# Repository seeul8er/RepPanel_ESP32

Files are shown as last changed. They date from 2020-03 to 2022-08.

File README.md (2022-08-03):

# RepPanel

## New Version HWv2 available
[Check out the new version RepPanel HWv2 for RepRap-based 3D Printers! Improved performance with ready to flash hardware from your local supplier.](https://reppanel.com)

## Older HWv1 version
A simple user interface for Duet/RepRap based 3D printers. Optimized for 3.5" touch
panels controlled via SPI & I²C using an ESP32.

Supports wireless connection or wired via UART/PanelDue port.

An open source alternative to the PanelDue.
  - Cheap (~18€ display + 7€ ESP32)
  - Beautifully dark
  - Compact and easy to use
  - Support for most operations required to set up a 3D print
  - Wireless connection - portable with power bar
  - PanelDue-port/UART connection

The all-in-one module is currently not available but you can give me an idea on how much interest there is. The module will be ready to use and thinner than a DIY solution. It includes a custom board, display and more capable ESP32 (more storage for directory listings etc.). I would try to get the price somewhere ~50-60€ + shipping from Germany. Click the link above and enter your email to get notified when a module becomes available. Thanks!

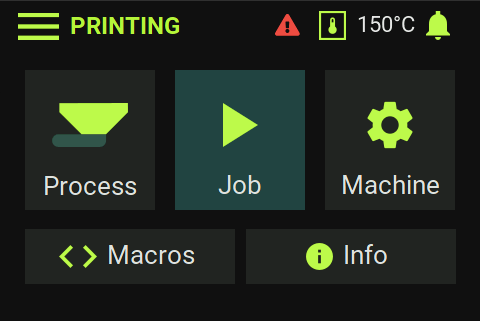
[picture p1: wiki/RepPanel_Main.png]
RepPanel main menu


## Features
Since RepPanel boots in ~1 second you can start setting up your printer in no time and with no additional hardware.
No need to get the laptop and log in to DuetWebControl. No need to get mad over using WebControl in your smartphones
browser.

 - Start, Stop, Pause & Resume print jobs based of Duets SD card
 - Simulate print jobs
 - Delete print jobs
 - Run macros (no dictionary support yet)
 - Home X, Y, Z or All axis
 - Set extruder fan speed
 - Load/Unload filament per tool
 - Set bed temperatures
 - Set tool temperatures
 - Monitor temperatures
 - Monitor print job:
   - Percent complete
   - Duration
   - Elapsed time (based of simulation, otherwise from file)
   - Job name
   - Current layer
 - Run manual and automated bed leveling
 - Automatic reconnection
 - Low latency
 - Screen Saver feature
 - Support for RRF 3.4+ Object Model

First release of RepPanel (https://youtu.be/FfghWz1Lrw4)  
First test of RepPanel (https://www.youtube.com/watch?v=39FKTUVjrxc)

## What this project is not
A full replacement for the DuetWebControl interface.

## Supported Hardware/Software
The RepPanel project is based on the [LVGL port for the ESP32](https://github.com/lvgl/lv_port_esp32/tree/c1f43bfb090df293059ab52baabbdbdd8df00712).
In theory this means all displays and touch controllers supported by the **lv_port_esp32** project are also supported
by RepPanel.

### Tested Hardware
The listed hardware below is tested and pre-compiled images are available under GitHub releases.

#### Hardware v1 (HWv1) platform
  - ESP32 DevKit without external RAM
  - [ER-TFTM035-6 display with capacitive touch screen, 4-Wire SPI, No font chip required](https://www.buydisplay.com/lcd-3-5-inch-320x480-tft-display-module-optl-touch-screen-w-breakout-board)

**Beware:** There are numerous version of the ER-TFT035-6. You must choose the one with the SPI interface. Do not get the arduino shield version (no SPI config). The version with the screen breakout board is sufficient.**  
Other display modules with a resolution of 480x320 should also work as long as they are supported by `lv_port_esp32`  
As of now RepPanel is optimized for 3.5" displays with a resolution of 480x320 pixels. The display is connected via SPI.

#### Hardware v2 (HWv2) platform
  - coming soon
  
### Differences between HWv1 & HWv2
coming soon

**Tested Firmware**
  - Duet2 WiFi running RepRap Firmware v3.0, v3.1, v3.2, v3.3 and corresponding Duet2WebControl
  - Duet3D + SBC is not supported via Wifi - only via the PanelDue serial port (wired connection)

## Installation
Use ready made images or compile yourself.

### Compile yourself

#### Set up ESP-IDF

[Follow instructions](https://docs.espressif.com/projects/esp-idf/en/v4.0/get-started/index.html#step-1-install-prerequisites) on offical Espressif site.  
ESP-IDF v4.0 is officially supported. ESP-IDF v4.3 is officially supported for the HWv2 electronics platform.

#### Clone Project

```bash
git clone --recurse-submodules https://github.com/seeul8er/RepPanel_ESP32
```
LVGL v7 is not supported. Last tested release of `lv_port_esp32` is commit `a76a3d5d9225d0cfb92c896b6b0f1867b62aa2b6`.
The project is linked against a fork to keep the legacy support and be able to fix bugs.

#### Configure Project

From its root run:
```bash
idf.py menuconfig
```
Under ``Component configuration`` you can change the supported TFT and Touchcontroller configuration and RepPanel 
specific settings.  

**See [Custom LVGL port for the ESP32](https://github.com/seeul8er/lv_port_esp32/tree/c1f43bfb090df293059ab52baabbdbdd8df00712) for further and more detailed instructions.**

#### Compile & Flash
```bash
idf.py build
idf.py -p (YOUR PORT) flash
```
**See [LVGL port for the ESP32](https://github.com/lvgl/lv_port_esp32/tree/c1f43bfb090df293059ab52baabbdbdd8df00712) for further and more detailed instructions.**

### Use ready made images
Ready made images are only available for selected hardware combinations! Please compile the project by yourself in
case you use different hardware or want a different pin connection layout

Check out [releases](https://github.com/seeul8er/RepPanel_ESP32/releases) for compiled binaries.

### Wiring ER-TFTM035-6 to the ESP32 DevKit (HWv1)

**Beware:** The available development boards have different pin configurations. Some have GND & 3.3V at the bottom. Others at the top.

Pin configuration of ready made images:
| **Pin Number ESP32 ** |  **Pin Number ER-TFTM035-6** | **Function** | **Description** | 
|:---:|:--:|:---: |:---: |
| VCC 3.3V |  2 | Power supply | Match TFT voltage with ESP32 pin | 
| GND | 1  | GND | Ground | 
| GPIO 13 | 27 | MOSI | Data line to TFT | 
| GPIO 14 | 24 | SCL | SPI CLK for TFT | 
| GPIO 15 | 23 | Slave Select | SPI | 
| GPIO 22 | 30 | SCL | I²C - touch | 
| GPIO 21 | 31 | SDA | I²C - touch | 
| GPIO 4 | 21 | Reset | TFT related | 
| GPIO 2 | 25 | Data | TFT related | 
| GPIO 27 | 29 | Backlight | Turn on/off TFT backlight | 
| GPIO 17 |  - | UART TX | Connect to RX PanelDue port  | 
| GPIO 16 |  - | UART RX | Connect to TX PanelDue port  |

## Screenshots
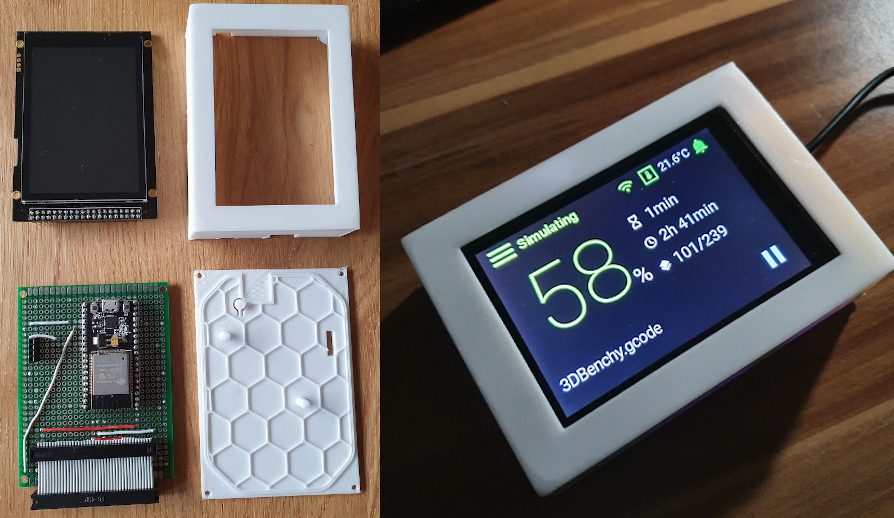
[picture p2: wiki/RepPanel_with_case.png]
RepPanel with case

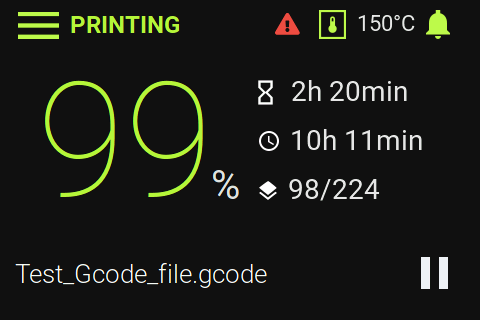
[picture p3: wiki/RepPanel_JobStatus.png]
RepPanel print job status

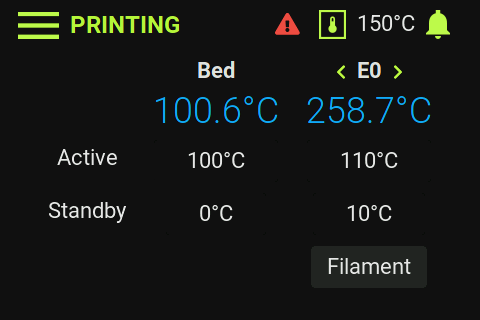
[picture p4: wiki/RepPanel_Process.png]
RepPanel process menu

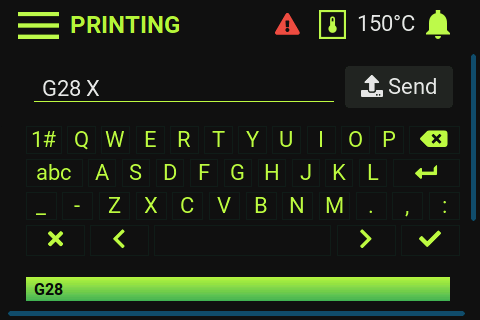
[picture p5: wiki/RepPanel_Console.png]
RepPanel console

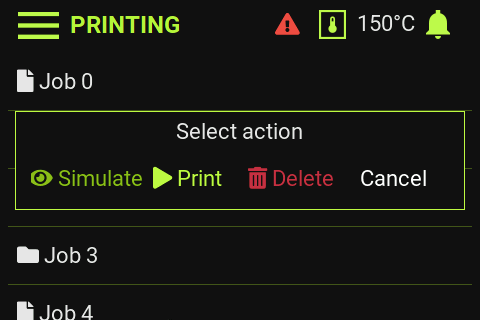
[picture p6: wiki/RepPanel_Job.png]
RepPanel start print dialog


## For Developers
[Check out the simulator project.](https://github.com/seeul8er/RepPanel_sim) Simulates the RepPanel GUI on Desktop computers for more efficient testing and implementation.

Use the provided for of lvgl for ESP32. This one contains the supported version of LVGL with some additional config options regarding the screen saver timeout. It is the only one maintained for RepPanel.

**Custom changes to lv_conf.h**  
Copy file content of `main/lv_conf_back.h` over to `externals/lv_port_esp32/components/lvgl/lv_conf.h`.  
Or simply add:
- Set `LV_USE_USER_DATA 1`
- Set `LV_MEM_SIZE    (17U * 1024U)` to free up unused RAM
- Add `#define LV_USE_THEME_REP_PANEL_DARK 1`
- `CONFIG_LVGL_FONT_ROBOTO16` & `CONFIG_LVGL_FONT_ROBOTO22` must be activated
- Add
```C
#define LV_FONT_CUSTOM_DECLARE  LV_FONT_DECLARE(reppanel_font_roboto_bold_16) \
                                       LV_FONT_DECLARE(reppanel_font_roboto_bold_18) \
                                       LV_FONT_DECLARE(reppanel_font_roboto_bold_24) \
                                       LV_FONT_DECLARE(reppanel_font_roboto_regular_26) \
                                       LV_FONT_DECLARE(reppanel_font_roboto_light_26) \
                                       LV_FONT_DECLARE(reppanel_font_roboto_thin_numeric_160) \
                                       LV_FONT_DECLARE(reppanel_font_roboto_regular_percent_40)
```

**Compilation options for different hardware platforms**
- esp-idf 4.0.x for ER-TFTM035-6 and other ILI9488 based displays (later esp-idf versions cause rendering artifacts)
- esp-idf 4.0.x or 4.3.x for ST7796s based displays

## Known Limitations
- Multiple tools supported but not tested
- Auto swap from UART to WiFi connection might take up to 10s
- Entries per directory listing limited to 24 for jobs and macros for ESP32 modules without external RAM
- Directory path limited to 160 characters for ESP32 modules without external RAM
- Filament listing (all filament names separated by one character) limited to 1014
- No support for Duet3 + SBC via Wifi because of a different API
  - Workaround: Use wired UART/PanelDue connection
- Can not list all files within a directory in case DuetWebControl API requires multiple requests per listing
  - Workaround: Delete files to reduce file count to make all files fit within one response

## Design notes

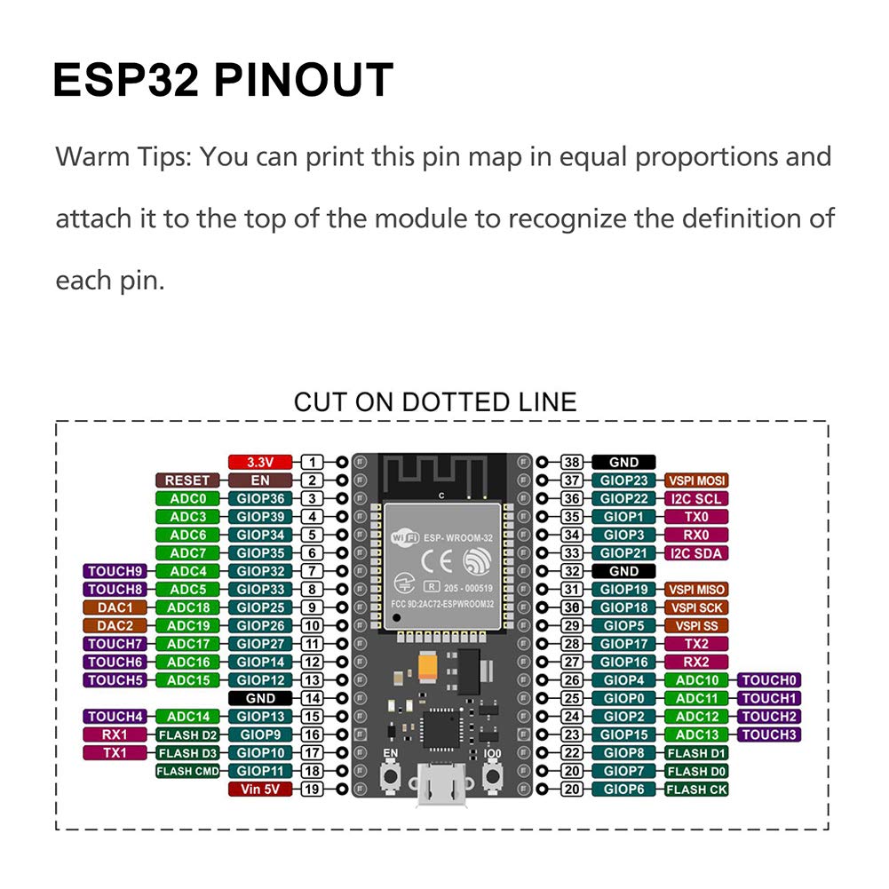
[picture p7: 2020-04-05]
wiki/NodeMCU_ESP32_Pinout.jpg

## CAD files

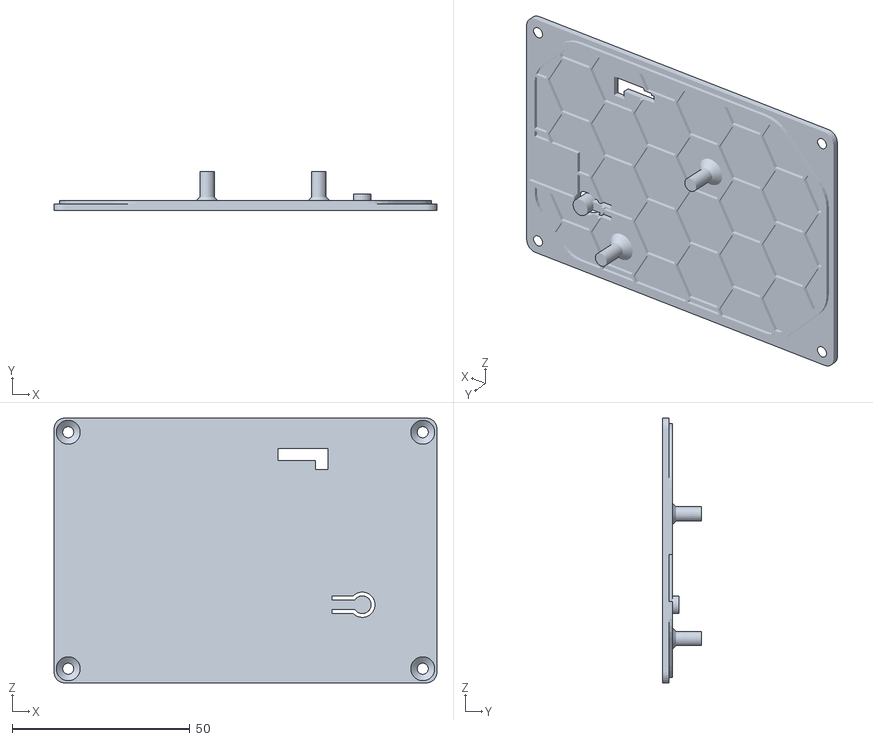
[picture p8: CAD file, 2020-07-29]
case/reppanelcover_back_v1_3.stl
107.7 x 10.9 x 74.5

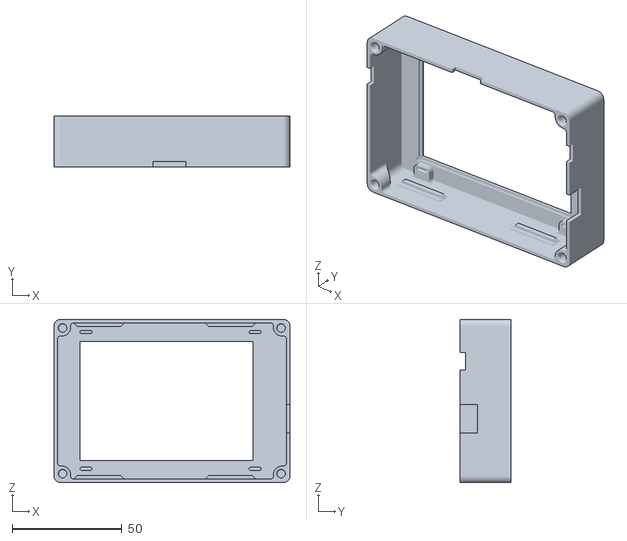
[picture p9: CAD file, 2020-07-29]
case/reppanelcover_front_v1_3.stl
107.7 x 23.4 x 74.5

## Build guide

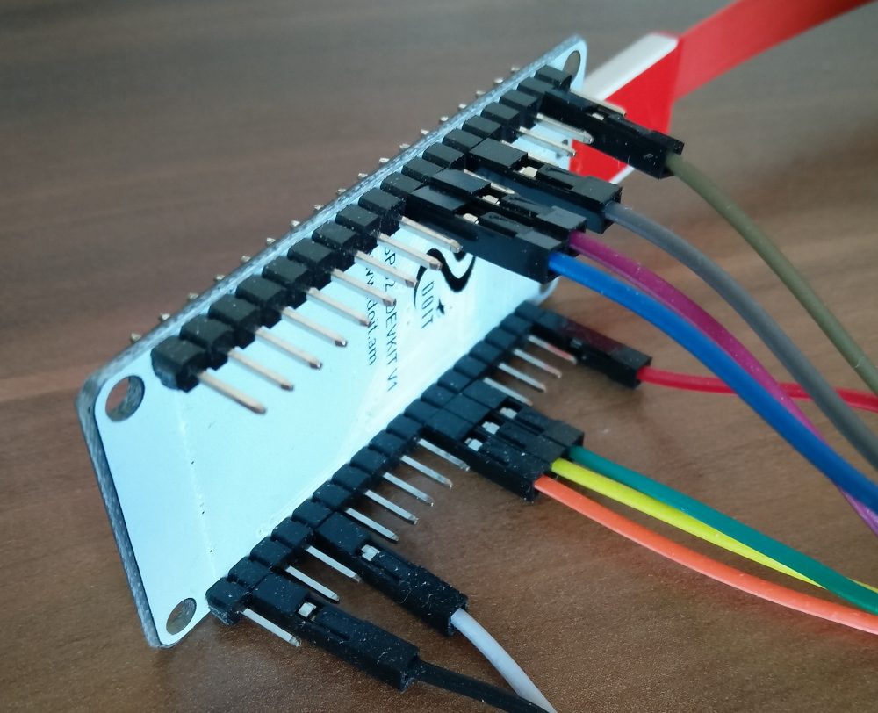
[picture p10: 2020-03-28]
wiki/Wiring_ESP32_DevKit_38GPIOs.jpg

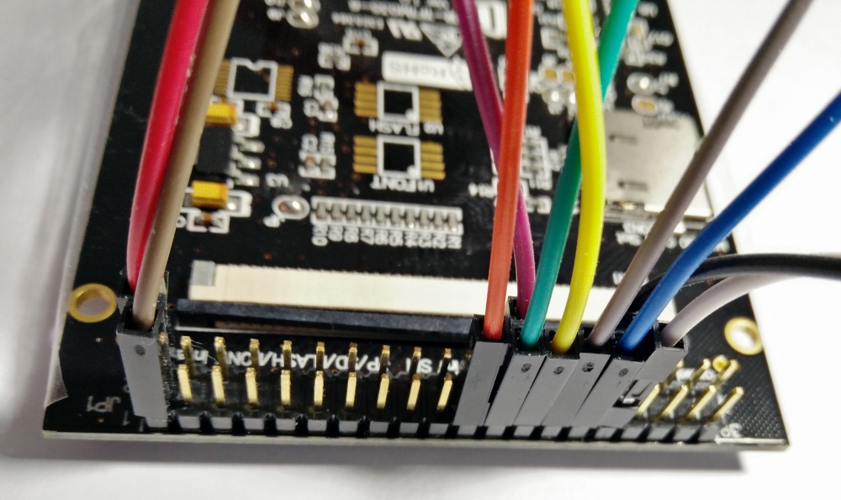
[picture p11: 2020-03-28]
wiki/Wiring_ERTFT.jpg

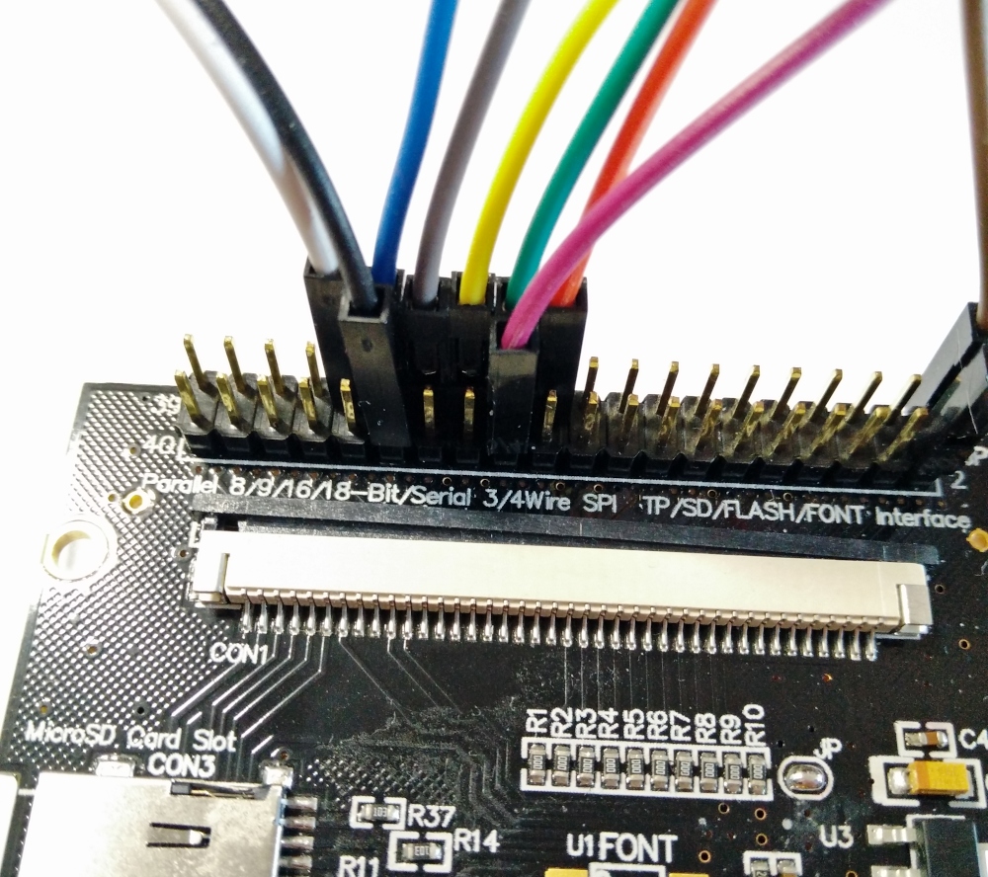
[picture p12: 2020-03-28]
wiki/Wiring_ERTFT_2.jpg

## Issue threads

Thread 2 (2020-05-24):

wiring issue

cdedwards, 2020-05-24:
Could you maybe give actual pin numbers on the tft panel in the following diagram?
http://prntscr.com/smmjlo

The ESP32 device I have and the nice ESP32_ Pinout diagram do not match at all. As well, the wiring pictures seem to be slightly out of sync compared to the diagrams. for example, the brown wire on the TFT picture goes to a NON ground pin on the ESP32.. Whereas the green wire, is hooked up to a "ground" on the ESP32, is not hooked to a ground on the TFT.

seeul8er, 2020-05-24:
The picture with the wiring relates to a [ESP32 DoIt Dev kit](https://i2.wp.com/randomnerdtutorials.com/wp-content/uploads/2018/08/ESP32-DOIT-DEVKIT-V1-Board-Pinout-36-GPIOs-updated.jpg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).
I think I will remove the pictures since they can cause more confusion than help clarifying the issue. There are just too many different board layouts for ESP32 dev kits.

I'll update the table as well to match with the ER-TFT module. [Check out page 11 on the docs](https://www.buydisplay.com/download/manual/ER-TFTM035-6_Datasheet.pdf) for details till then.

seeul8er, 2020-05-24:
Updated README

Closed 2020-05-24.

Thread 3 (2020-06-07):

FT6X36: Error reading from device: ERROR

tunip, 2020-06-07:
Hi,

flashed the newest version (1.0.1) to my ESP32 (https://www.amazon.de/gp/product/B07PG923ZK/ref=ppx_yo_dt_b_search_asin_title?ie=UTF8&psc=1)

Checked wires, should be fine. If I start the ESP32 I see the following message:

```
[15:32:35]I (210) ILI9488: ILI9488 initialization.
[15:32:36]I (510) ILI9488: Enabling backlight.
[15:32:36]I (510) FT6X36: Found touch panel controller
[15:32:36]E (510) FT6X36: Error reading from device: ERROR
[15:32:36]I (510) FT6X36: 	Device ID: 0x00
[15:32:36]I (520) FT6X36: 	Chip ID: 0x00
[15:32:36]I (520) FT6X36: 	Device mode: 0x00
[15:32:36]I (530) FT6X36: 	Firmware ID: 0x00
[15:32:36]I (530) FT6X36: 	Release code: 0x00
```

Any idea what can I check?

Display is showing only a white screen after start.

PS: Checked another ESP32 (LOLIN D32) same error with white screen.

seeul8er, 2020-06-07:
Should be a wiring issue.

Are you using the ER-TFT?
Can you post your wiring?
Did you compile yourself or use the provided image?

tunip, 2020-06-07:
OK, rewired it again.

Yes, it is a ER-TFTM035-6 display.

Wiring is exactly from the README.md:
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

Did a try with the provided image and now I also tried a compile by my self. Both are the same issue.

Will try different cables. Maybe the one is faulty.

seeul8er, 2020-06-07:
Can you post an image of the back of your TFT board? From your pictures it looks like you got one that is in "8080 16-bit Interface" configuration. The ESP32/RepPanel only supports SPI displays as for now.
You need a board with 4 Wire SPI (3 wire should work as well but untested) and the capacitive touch screen. Font chip is not required.
See [https://www.buydisplay.com/download/manual/ER-TFTM035-6_Datasheet.pdf](https://www.buydisplay.com/download/manual/ER-TFTM035-6_Datasheet.pdf) Section 4.3

However, you should be able to "transform/hack" your board to be in 4 wire config. That would require you to solder/desolder some jumpers and resistors. Not sure that is worth the trouble.

tunip, 2020-06-07:
Back of the TFT board. Did not know of the different variants of the ER-TFTM035-6.

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

In the package, there was also an Arduino Shield.

seeul8er, 2020-06-08:
Yes, definitley not the SPI version. The yellow ribbon cable is also missing the capacitive touch panel chip. Found it on ebay as well. Ebay is a lot more confusing than their dedicated website.

Sorry for that, I'll make sure to update the README so that others do not make the same mistake.
I'll close this issue for now. Do not hesitate to open a new one when there are problems with the new board.

Closed 2020-06-08.

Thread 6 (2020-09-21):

JSON buffer too small if json response contains larger structure

oliof, 2020-09-21:
Just got RepPanel up and running thanks to PCR's great board. But the board crashed repeatedly after connecting my panel to the Duet2Wifi machine I tested again. Serial monitor shows:

```
 [0;32mI (9203) RequestTask: Downloading 0%3A%2Fsys%2Fdwc2settings.json [0m
 [0;32mI (9213) RequestTask: Downloading http://192.168.86.35/rr_download?name=0%3A%2Fsys%2Fdwc2settings.json [0m
 [0;31mE (9383) RequestTask: Status-JSON buffer overflow (4241 >= 4096). Resetting! [0m
 [0;31mE (9413) RequestTask: Status-JSON buffer overflow (4456 >= 4096). Resetting! [0m
 [0;31mE (9463) RequestTask: Status-JSON buffer overflow (4096 >= 4096). Resetting! [0m
 [0;32mI (9473) RequestTask: Status = 200, content_length = 14458 [0m
 [0;32mI (9473) RequestTask: Processing D2WC status json [0m
Guru Meditation Error: Core  1 panic'ed (LoadProhibited). Exception was unhandled.
```

Downloading dwc2settings.json and inspecting it showed that the machine/codes array had many entries. The crash meant that RepPanel hadn't closed it's handle correctly, so the file was open and I couldn't edit it without restarting the printer.

Deleting the contents of machine/codes in dwc2settings.json (it's used for auto-completion in DWC which I've disabled anyways, so arguably this is an error on DWC's side, but some people use it and may have arbitrarily large numbers of entries here ) made the RepPanel crashes stop.

Suggested solution: Handle the error gracefully.

Sample json file to reproduce the issue attached (zipped).

[settings.zip](https://github.com/seeul8er/RepPanel_ESP32/files/5257611/settings.zip)

seeul8er, 2020-09-22:
Thank you for the detailed bug report! I'll take a look at it.

seeul8er, 2022-01-01:
The ESP32 WROOM does not provide enought RAM for a big JSON response. The ESP32 WROVER can solve the issue with the additional external RAM. Can be fixed with updated hardware.

Closed 2022-01-01.

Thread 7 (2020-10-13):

how to calibration touch sensor

minhngoc123, 2020-10-13:
hello,how to calibration touch sensor,i setting and upload but touch sensor work not fine

seeul8er, 2020-10-13:
The recommended hardware does not need touch sensor calibration. If you compile it for a different hardware you can calibrate the touch sensor via the LVGL settings in menuconfig step

Closed 2020-10-14.

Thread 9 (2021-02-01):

System crash when no filament is specified

seeul8er, 2021-02-01:
RepPanel crashes when Duet has no filament defined

seeul8er, 2022-01-01:
Needs testing if still an issue

seeul8er, 2022-01-29:
Should be fixed

Closed 2022-01-29.

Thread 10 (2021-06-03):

Crash when accessing "Job"

iz3man, 2021-06-03:
Soldered everyting together yesterday and installed latest precompiled firmware to my Wemos32.
Everything worked instantly. I can connect to the printer and send G commands etc.

But when I press "Job" this leads to an instand reboot of the ESP.

See attached video: https://youtu.be/_Eae3WFpU4Y

seeul8er, 2021-06-03:
How many jobs are listed in the root directory?

iz3man, 2021-06-03:
28

seeul8er, 2021-06-03:
There you have it. Because we a running low on RAM, [RepPanel is limited to 16 items per listing](https://github.com/seeul8er/RepPanel_ESP32#known-limitations). I suggest you reduce your item count per directory (<16) by adding more subfolders.

iz3man, 2021-06-04:
That's a shame. Should have read the readme more carefully. This renders the device pretty useless. putting everything into subdirectories makes it a mess. And if I got 16 subfolders I need subfolders for subfolders?
Any solution for this? Other ESP?

seeul8er, 2021-06-04:
Yes. RepPanel can list 16 entries per directory (folders + files <=16)
Right now I have no ambition to squeeze more out of it since the system will get more unstable when bigger parts of the screen need an update (requires more RAM).
I have some ideas for [a new/custom board that features an ESP32 with attached 4/8MB of external RAM](https://docs.google.com/forms/d/e/1FAIpQLSc41e0SKuG6xnuFPz0I5em8UYw0sTvzpZe8-aQhP_QksgwWyg/viewform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). That would eliminate most of the limitations we have with the DEV-Board based setups. However, as of today, only a single person showed interest so I am currently not pushing into that direction, since it also requires some $/€/time invest from my side to get it working.

Closed 2021-06-04.

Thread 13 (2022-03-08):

Crash when printer requires password, but no password configured in RepPanel

seeul8er, 2022-03-08:
In v1.4.0

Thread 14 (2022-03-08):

Crash when setting fan speed in HWv2

seeul8er, 2022-03-08:
Stack overflow in GUI task.

Closed 2022-05-31.

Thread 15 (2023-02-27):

Blank Screen After reflashing

chanyork, 2023-02-27:
Hello,  I believe I have a HWV1.  After reflashing my RepPanel screen is blank.  Please help.

chanyork, 2023-02-28:
by the way the flash was successful.  it become blank once i erase the firmware.  and after that reflash nothing on screen

chanyork, 2023-02-28:
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
Attached is my board .

seeul8er, 2023-02-28:
You are using v2 Hardware. I will contact you via email, since this is the git for the HWv1 release :)

Closed 2023-02-28.

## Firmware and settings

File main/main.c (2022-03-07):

#include <sys/cdefs.h>
//
// Copyright (c) 2020 Wolfgang Christl
// Licensed under Apache License, Version 2.0 - https://opensource.org/licenses/Apache-2.0

#include <stdbool.h>
#include <stdio.h>
#include <stdlib.h>
#include <nvs_flash.h>
#include <esp_log.h>

#include "freertos/FreeRTOS.h"
#include "freertos/task.h"
#include "esp_freertos_hooks.h"
#include "freertos/semphr.h"
#include "esp_system.h"

/* Littlevgl specific */
#include "lvgl/lvgl.h"
#include "lvgl_driver.h"
#include "reppanel.h"
#include "esp32_wifi.h"
#include "reppanel_request.h"
#include "esp32_uart.h"
#include "rrf_objects.h"
#include "screen_saver.h"

#ifdef CONFIG_REPPANEL_ENABLE_QOI_THUMBNAIL_SUPPORT
#define QOI_IMPLEMENTATION
#define QOI_NO_STDIO
#include "../externals/qoi/qoi.h"
#endif

#ifdef CONFIG_LVGL_TFT_DISPLAY_MONOCHROME
#include "lv_theme_mono.h"
#endif
#define TAG "Main"

SemaphoreHandle_t xGuiSemaphore;
double reprap_chamber_temp_buff[NUM_TEMPS_BUFF] = {0};
int reprap_chamber_temp_curr_pos = 0;
double reprap_babysteps_amount = 0.05;
double reprap_move_feedrate = 6000;
double reprap_mcu_temp = 0;
char reprap_firmware_name[32];
char reprap_firmware_version[5];

static void IRAM_ATTR lv_tick_task(void *arg);

_Noreturn void guiTask();

/**********************
 *   APPLICATION MAIN
 **********************/
void app_main() {
    //If you want to use a task to create the graphic, you NEED to create a Pinned task
    //Otherwise there can be problem such as memory corruption and so on
    xTaskCreatePinnedToCore(guiTask, "gui", CONFIG_REPPANEL_GUI_TASK_STACK_SIZE, NULL, 0, NULL, 1);

    TaskHandle_t printer_status_task_handle = NULL;
    xTaskCreate(request_reprap_status_updates, "Printer Status Update Task", CONFIG_REPPANEL_REQUEST_TASK_STACK_SIZE, NULL,
                tskIDLE_PRIORITY, &printer_status_task_handle);
    configASSERT(printer_status_task_handle);
}

static void IRAM_ATTR lv_tick_task(void *arg) {
    (void) arg;
    lv_tick_inc(portTICK_RATE_MS);
}

_Noreturn void guiTask() {
    /* Inspect our own high water mark on entering the task. */
//    UBaseType_t uxHighWaterMark = uxTaskGetStackHighWaterMark( NULL );
    xGuiSemaphore = xSemaphoreCreateMutex();
    lv_init();
    lvgl_driver_init();

    static lv_color_t buf1[DISP_BUF_SIZE];
    static lv_color_t buf2[DISP_BUF_SIZE];
    static lv_disp_buf_t disp_buf;
    lv_disp_buf_init(&disp_buf, buf1, buf2, DISP_BUF_SIZE);

    lv_disp_drv_t disp_drv;
    lv_disp_drv_init(&disp_drv);
    disp_drv.flush_cb = disp_driver_flush;
#ifdef CONFIG_LVGL_TFT_DISPLAY_MONOCHROME
    disp_drv.rounder_cb = disp_driver_rounder;
    disp_drv.set_px_cb = disp_driver_set_px;
#endif

    disp_drv.buffer = &disp_buf;
    lv_disp_t *lcd_display = lv_disp_drv_register(&disp_drv);

#if defined CONFIG_LVGL_TFT_DISPLAY_MONOCHROME
    lv_theme_mono_init(0, NULL);
    lv_theme_set_current( lv_theme_get_mono() );
#endif

#if CONFIG_LVGL_TOUCH_CONTROLLER != TOUCH_CONTROLLER_NONE
    lv_indev_drv_t indev_drv;
    lv_indev_drv_init(&indev_drv);
    indev_drv.read_cb = touch_driver_read;
    indev_drv.type = LV_INDEV_TYPE_POINTER;
    lv_indev_drv_register(&indev_drv);
#endif

    const esp_timer_create_args_t periodic_timer_args = {
            .callback = &lv_tick_task,
            /* name is optional, but may help identify the timer when debugging */
            .name = "periodic_gui"
    };
    esp_timer_handle_t periodic_timer;
    ESP_ERROR_CHECK(esp_timer_create(&periodic_timer_args, &periodic_timer));
    //On ESP32 it's better to create a periodic task instead of esp_register_freertos_tick_hook
    ESP_ERROR_CHECK(esp_timer_start_periodic(periodic_timer, 10 * 1000)); //10ms (expressed as microseconds)


    init_reprap_buffers();

    //Initialize NVS
    esp_err_t ret = nvs_flash_init();
    if (ret == ESP_ERR_NVS_NO_FREE_PAGES || ret == ESP_ERR_NVS_NEW_VERSION_FOUND) {
        ESP_ERROR_CHECK(nvs_flash_erase());
        ret = nvs_flash_init();
    }
    ESP_ERROR_CHECK(ret);
    init_reprap_model();
    read_settings_nvs();
    rep_panel_ui_create();
#if defined(CONFIG_REPPANEL_ESP32_WIFI_ENABLED)
#if ESP_IDF_VERSION_MAJOR == 4 && ESP_IDF_VERSION_MINOR == 3
    wifi_init_sta_4_3();
#else
    wifi_init_sta();
#endif
#endif
    init_uart();

//    int c = 0;
//    lv_mem_monitor_t m;
    while (1) {
        vTaskDelay(1);

//        lv_mem_monitor(&m);
//        UBaseType_t uxHighWaterMark = uxTaskGetStackHighWaterMark(NULL);
//        if (c%50) {
//            ESP_LOGI(TAG, "%i free bytes in GUI, %i%% used, %i high mark of GUI Task", m.free_size, m.used_pct,
//                     uxHighWaterMark);
//            c = 0;
//        } else { c++; }

        //Try to lock the semaphore, if success, call lvgl stuff
        if (xSemaphoreTake(xGuiSemaphore, (TickType_t) 10) == pdTRUE) {
            lv_task_handler();
            // handle screen saver stuff
            if (lv_disp_get_inactive_time(lcd_display) > (CONFIG_REPPANEL_SCREEN_SAVER_TIMEOUT * 1000)) {
                activate_screen_saver();
            } else {
                deactivate_screen_saver();
            }
            xSemaphoreGive(xGuiSemaphore);
        }
    }
    // This task should NEVER return
    vTaskDelete(NULL);
}

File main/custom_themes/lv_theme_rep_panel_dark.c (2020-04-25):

//
// Copyright (c) 2020 Wolfgang Christl
// Licensed under Apache License, Version 2.0 - https://opensource.org/licenses/Apache-2.0

/*********************
 *      INCLUDES
 *********************/
#include <lvgl/src/lv_core/lv_style.h>
#include <lvgl/lvgl.h>
#include "lvgl/src/lv_themes/lv_theme.h"
#include "lv_theme_rep_panel_dark.h"

#if LV_USE_THEME_REP_PANEL_DARK

/*********************
 *      DEFINES
 *********************/
#define DEF_RADIUS 2
#define DEF_SHADOW_COLOR lv_color_hex3(0x000)

/**********************
 *      TYPEDEFS
 **********************/

/**********************
 *  STATIC PROTOTYPES
 **********************/

/**********************
 *  STATIC VARIABLES
 **********************/
static lv_theme_t theme;
static lv_style_t def_style;

/*Static style definitions*/
static lv_style_t sb;

/*Saved input parameters*/
static uint16_t _hue;
static lv_font_t *_font;

/**********************
 *      MACROS
 **********************/

/**********************
 *   STATIC FUNCTIONS
 **********************/

static void basic_init(void) {
    static lv_style_t bg, panel, scr;

    lv_style_copy(&def_style, &lv_style_plain); /*Initialize the default style*/
    def_style.text.font = _font;
    def_style.body.radius = DEF_RADIUS;
    def_style.body.main_color = REP_PANEL_DARK;

    lv_style_copy(&bg, &def_style);
    bg.body.main_color = REP_PANEL_DARK;        // 0x2c3e50
    bg.body.grad_color = bg.body.main_color;
    bg.body.radius = 0;

    lv_style_copy(&scr, &bg);
    scr.body.padding.bottom = 0;
    scr.body.padding.top = 0;
    scr.body.padding.left = 0;
    scr.body.padding.right = 0;

    lv_style_copy(&panel, &def_style);
    panel.body.radius = 0;
    panel.body.main_color = REP_PANEL_DARK;
    panel.body.grad_color = REP_PANEL_DARK;
    panel.body.border.width = 0;
    panel.body.border.color = lv_color_hex3(0xbbb);
    panel.body.border.opa = LV_OPA_COVER;
    panel.body.shadow.color = DEF_SHADOW_COLOR;
    panel.body.shadow.type = LV_SHADOW_BOTTOM;
    panel.body.shadow.width = 0;
    panel.body.padding.left = LV_DPI / 12;
    panel.body.padding.right = LV_DPI / 12;
    panel.body.padding.top = LV_DPI / 25;
    panel.body.padding.bottom = LV_DPI / 50;
    panel.body.padding.inner = LV_DPI / 9;
    panel.text.color = REP_PANEL_DARK_TEXT;
    panel.image.color = REP_PANEL_DARK_TEXT;

    lv_style_copy(&sb, &def_style);
    sb.body.main_color = REP_PANEL_DARK_HIGHLIGHT;
    sb.body.grad_color = REP_PANEL_DARK_HIGHLIGHT;
    sb.body.opa = LV_OPA_40;
    sb.body.padding.right = LV_DPI / 25;
    sb.body.padding.bottom = LV_DPI / 25;

    theme.style.bg = &bg;
    theme.style.scr = &scr;
    theme.style.panel = &panel;

    static lv_style_t style_prr;
    lv_style_copy(&style_prr, &lv_style_plain);
    style_prr.body.main_color = REP_PANEL_DARK;
    style_prr.body.grad_color = REP_PANEL_DARK;
    lv_obj_set_style(lv_scr_act(), &style_prr);
}

static void cont_init(void) {
#if LV_USE_CONT != 0

    theme.style.cont = theme.style.panel;
#endif
}

static void btn_init(void) {
#if LV_USE_BTN != 0
    static lv_style_t rel, pr, tgl_rel, tgl_pr, ina;

    lv_style_copy(&rel, &def_style);
    rel.body.main_color = REP_PANEL_DARK_ACCENT_GREY;
    rel.body.grad_color = REP_PANEL_DARK_ACCENT_GREY;
    rel.body.radius = DEF_RADIUS;
    rel.body.padding.left = LV_DPI / 6;
    rel.body.padding.right = LV_DPI / 6;
    rel.body.padding.top = LV_DPI / 12;
    rel.body.padding.bottom = LV_DPI / 12;
    rel.body.padding.inner = LV_DPI / 10;
    rel.body.shadow.color = DEF_SHADOW_COLOR;
    rel.body.shadow.type = LV_SHADOW_BOTTOM;
    rel.body.shadow.width = 0;
    rel.body.border.color = REP_PANEL_DARK_TEXT;
    rel.body.border.width = 0;
    rel.text.color = REP_PANEL_DARK_TEXT;
    rel.image.color = lv_color_hsv_to_rgb(_hue, 5, 95);

    lv_style_copy(&pr, &rel);
    pr.body.main_color = REP_PANEL_DARK;
    pr.body.grad_color = REP_PANEL_DARK;
    pr.text.color = REP_PANEL_DARK_ACCENT;
    pr.body.border.color = REP_PANEL_DARK_ACCENT;
    pr.body.border.width = 1;
    pr.body.shadow.width = 0;

    lv_style_copy(&tgl_rel, &rel);
    tgl_rel.body.main_color = REP_PANEL_DARK_ACCENT_ALT2;
    tgl_rel.body.grad_color = REP_PANEL_DARK_ACCENT_ALT2;
    tgl_rel.body.shadow.width = 0;

    lv_style_copy(&tgl_pr, &tgl_rel);
    tgl_pr.body.main_color = REP_PANEL_DARK_ACCENT_ALT1;
    tgl_pr.body.grad_color = REP_PANEL_DARK_ACCENT_ALT1;
    tgl_pr.body.shadow.width = 0;

    lv_style_copy(&ina, &rel);
    ina.body.main_color = lv_color_hex3(0xccc);
    ina.body.grad_color = ina.body.main_color;
    ina.body.shadow.width = 0;
    ina.text.color = REP_PANEL_DARK_TEXT;
    ina.image.color = lv_color_hsv_to_rgb(_hue, 95, 5);

    theme.style.btn.rel = &rel;
    theme.style.btn.pr = &pr;
    theme.style.btn.tgl_rel = &tgl_rel;
    theme.style.btn.tgl_pr = &tgl_pr;
    theme.style.btn.ina = &ina;
#endif
}

static void label_init(void) {
#if LV_USE_LABEL != 0
    static lv_style_t prim, sec, hint;

    lv_style_copy(&prim, &def_style);
    prim.text.font = _font;
    prim.text.color = lv_color_hsv_to_rgb(_hue, 80, 100);

    lv_style_copy(&sec, &prim);
    sec.text.color = lv_color_hsv_to_rgb(_hue, 80, 210);

    lv_style_copy(&hint, &prim);
    hint.text.color = lv_color_hsv_to_rgb(_hue, 40, 255);

    theme.style.label.prim = &prim;
    theme.style.label.sec = &sec;
    theme.style.label.hint = &hint;
#endif
}

static void img_init(void) {
#if LV_USE_IMG != 0
    static lv_style_t img_light, img_dark;
    lv_style_copy(&img_light, &def_style);
    img_light.image.color = lv_color_hsv_to_rgb(_hue, 15, 85);
    img_light.image.intense = LV_OPA_80;

    lv_style_copy(&img_dark, &def_style);
    img_light.image.color = lv_color_hsv_to_rgb(_hue, 85, 65);
    img_light.image.intense = LV_OPA_80;

    theme.style.img.light = &def_style;
    theme.style.img.dark = &def_style;
#endif
}

static void line_init(void) {
#if LV_USE_LINE != 0

    theme.style.line.decor = &def_style;
#endif
}

static void led_init(void) {
#if LV_USE_LED != 0
    static lv_style_t led;
    lv_style_copy(&led, &def_style);
    led.body.shadow.width = LV_DPI / 10;
    led.body.radius = LV_RADIUS_CIRCLE;
    led.body.border.width = LV_DPI / 30;
    led.body.border.opa = LV_OPA_30;
    led.body.main_color = lv_color_hsv_to_rgb(_hue, 100, 100);
    led.body.grad_color = lv_color_hsv_to_rgb(_hue, 100, 100);
    led.body.border.color = lv_color_hsv_to_rgb(_hue, 60, 60);
    led.body.shadow.color = lv_color_hsv_to_rgb(_hue, 100, 100);

    theme.style.led = &led;
#endif
}
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

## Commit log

2020-03-11 Display wifi status, scan networks
    [partitions.csv]
2020-03-12 Working status request & WiFi config.
    [partitions.csv]
2020-03-18 Replaced drop down lists with button logic for process temperature
    [duet_status_json.h, lv_theme_rep_panel_light.c, main.c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]
2020-03-22 Job selection and status UI dummies. Fixed active/standby temp.
    General GUI improvements
    [duet_status_json.h, lv_theme_rep_panel_light.c, reppanel.h]
2020-03-22 Working job monitoring. Temp sync issue resolved (needs testing)
    [duet_status_json.h, main.c, reppanel.h]
2020-03-23 Fixed set temp bug
    [lv_theme_rep_panel_light.c]
2020-03-27 Various bugfixes. Individual response buffers for request tasks
    [reppanel_request.c]
2020-03-28 Added folder support for macros & jobs
    Sudden crashes when monitoring Job
    [main.c, reppanel.h]
2020-04-01 Fixed memory leak
    Reformated, Change to LV_EVENT_CLICKED, Request cleanup
    [esp32_wifi.c]
2020-04-04 Added support for bed leveling (needs testing)
    Added homing indicator
2020-04-05 Fixes for True Bed Calibration - still not working
    [reppanel.h, reppanel_request.c]
2020-04-06 Manual bed calibration working
2020-04-06 Updated Readme with wiring instructions
2020-04-11 Preparation for UART support
2020-04-15 UART implementation preview - needs testing
2020-04-25 UART testing around #1
2020-04-25 Fixed bug with latest esp-idf 4.0 release
    [esp32_wifi.c, lv_theme_rep_panel_dark.c, main.c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]
2020-04-25 UART connection working - proper state machine needed
    Resolving of mDNS address does not work anymore
    [duet_status_json.h, esp32_uart.c, esp32_wifi.c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]
2020-04-26 Fixing UART bugs WIP
    [esp32_uart.c, esp32_wifi.c, main.c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]
2020-05-01 Fixed job & macro request, fixed bed & tool temps with UART
    Bed & tool temps not working with WiFi again :(
    Tested with latest esp-idf 4.0
    [esp32_uart.c, esp32_wifi.c, main.c]
2020-05-02 proper mDNS resolve, Duet mDNS discovery, bugfixes with temps while Wifi
    [esp32_wifi.c, reppanel.h, reppanel_request.c]
2020-05-05 RC1 v1.0.0 - Fixed crashes due to low memory. Refractoring
    [main.c, reppanel.h]
2020-05-15 Fixed Wifi reconnect bug & mDNS resolve issue
    [esp32_wifi.c, reppanel_request.c]
2020-05-16 Release 1.0.0
    Fixed empty msg box.
    Fixed deactivate tool heater issue.
    Fixed tool temp update in UART mode
    [reppanel.h, reppanel_request.c]
2020-05-22 Fixed potential bug. Updated lv_port_esp32
    [reppanel_request.c]
2020-05-24 Fixed num_tools, added TFT-ER pin numbers, rearranged machine gui
    [reppanel.h, reppanel_request.c]
2020-06-10 Added README LVGL version notice. Fixed msgbox bug
    Reverse order for jobs in list
    [reppanel_request.c]
2020-06-22 Reduced animation time, reverted inverse file listing
    Higher stability due to faster scroll stop in lists. Lower amount of updates -> less RAM/DMA
    [reppanel.h]
2020-07-29 Added 3D print files for the case
    [reppanelcover_back_v1_3.stl, reppanelcover_front_v1_3.stl]
2020-08-03 chore(machine): add lightning/power/fan controls
2020-08-03 chore(lv): decrease LVGL memsize to offer more memory for DMA
2020-08-15 chore(panel): change console button icon, Keyboard icon by Rflor from the Noun Project (CC-BY-3.0-US)
2020-08-15 chore(machine): change power btn to toggle mode; change page layout
2020-08-22 Increased version number - light switch default off
2020-11-01 Fixed filament unload tool selection
2021-05-01 Fixed empty filament crash
    [esp32_wifi.c, reppanel.h, reppanel_request.c]
2021-05-02 Sort dir listings by modification date
    Fix for filament load error
    [reppanel.h, reppanel_request.c]
2021-11-06 changed default bed temperatures
2021-11-08 fixed compiler errors, added apilevel parser code
    [main.c, reppanel_request.c]
2021-11-09 Minor fixes. Wifi API version integration
    [reppanel.h, reppanel_request.c]
2021-11-10 tool temperatures WIP - in general working
2021-11-13 Debugging & testing - fan speed working
2021-11-17 FIxed print job status, percent and time left
    [reppanel_request.c]
2021-12-28 Fixed seq. numbers and extended refresh
    [reppanel_request.c]
2021-12-31 Fixed RRF2 msg box
    [esp32_uart.c, reppanel_request.c]
2022-01-01 RRF3 UART Object Model Debugging
2022-01-01 UART issues fixed. Ready for merge
    [esp32_uart.c, reppanel_request.c]
2022-01-29 Fixed memory bugs, massive stability improvements, more list items
    Increased list to 24 possible items
    Increased max file path length to 160 bytes
    Fixed memory bugs
    Added config options to configure RepPanel specific settings via menuconfig -> Component configuration
    [esp32_wifi.c, main.c, reppanel.h]
2022-02-07 Fixed bugs for all hardware platforms. Added HWv2 support
    No external RAM supported for now
    [main.c, reppanel_request.c]
2022-02-08 Fixed jobinfo bugs. Linked qoi-lib. Does not build
    [main.c, reppanel_request.c]
2022-02-24 fixed UART parser bug
    [esp32_uart.c]
2022-03-05 File info display job WIP
    UART works, Wifi not really. Sim time is wrong sometimes
    [reppanel_request.c]
2022-03-07 Fixed crashes and fileinfo
    Increased file info timeout
    Fixed crash when button is not clicked in dialog
    Removed Console header from import section
    fixed simulated time parsing
    fixed filament usage calculation
    [reppanel_request.c]
